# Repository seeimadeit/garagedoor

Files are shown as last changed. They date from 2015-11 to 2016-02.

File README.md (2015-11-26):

# Garage Door Opener

Project Status: Unstable - in development

 * circuit design - stable
* iphone software - unstable
* arduino software - unstable
* box housing - stable/regular changes

Project located @ 
[https://github.com/seeimadeit/garagedoor](https://github.com/seeimadeit/garagedoor "Github")
and [https://seeimadeit.wordpress.com/](https://seeimadeit.wordpress.com/ "Wordpress")

This hardware device is a simple Arduino based relay controller, it uses the Adafruit BLE nRF8001 [http://www.adafruit.com/products/1697](http://www.adafruit.com/products/1697 "Adafruit website").

Stuff I use to make it

* Hardware
	1. circuitboard Eagle CAD 7.4.0
	2. Housing Cubify Design 2014
* Software
	1. Apple XCode 7.1.x, Swift 2 - iPhone
	2. Arduino 1.6.5
	3. Libraries
		* MD5 - https://github.com/scottmac/arduino
		* BLE - https://github.com/sandeepmistry/arduino-BLEPeripheral

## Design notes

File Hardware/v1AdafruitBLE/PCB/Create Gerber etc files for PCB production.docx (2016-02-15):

Create Gerber etc files for PCB production

In eagle select the “Cam processor” from the File menu

After the cam processor has loaded from the File menu choose Open->Job

Load the garagedoor-gerb274x.cam file

The will be multiple tabs , each tab represents a section (or a file output).

It will look like this

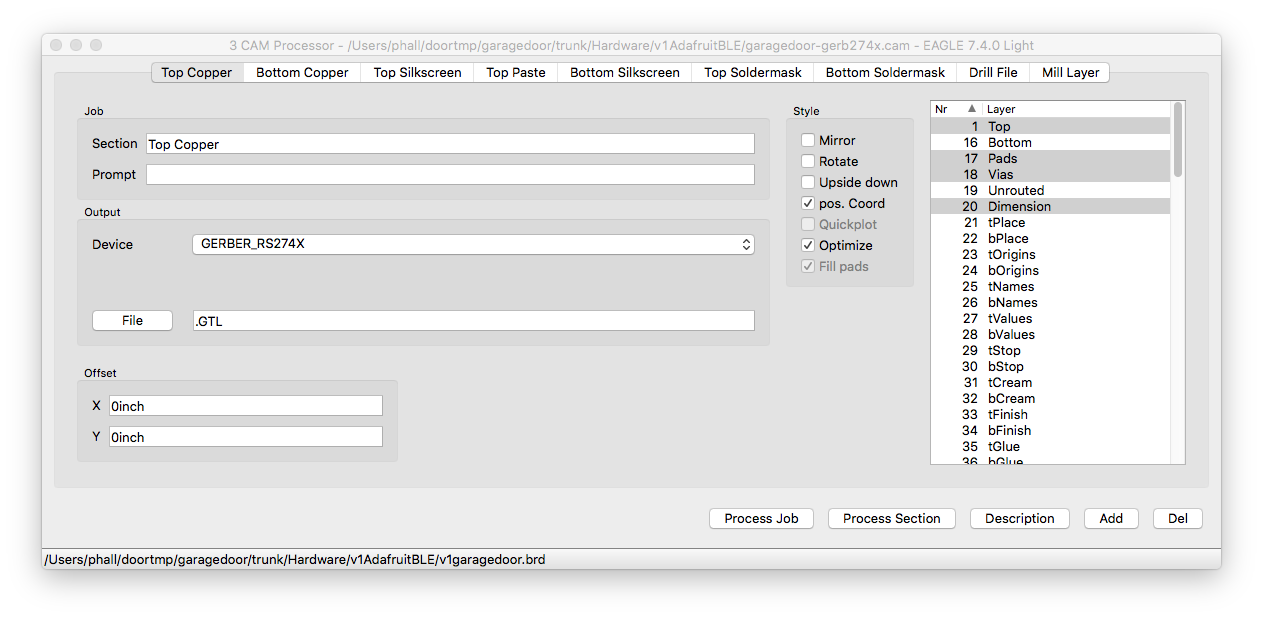
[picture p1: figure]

Click on each of the tab and review the settings to match the list below.

Click the ‘Process Job’ button to output the files.

Add the following files into a .ZIP file

V1garagedoor.dri

V1garagedoor.GBL

V1garagedoor.GBO

V1garagedoor.GBS

V1garagedoor.GML

V1garagedoor.GTL

V1garagedoor.GTO

V1garagedoor.GTP

V1garagedoor.GTS

V1garagedoor.TXT

Submitting to advanced circuits

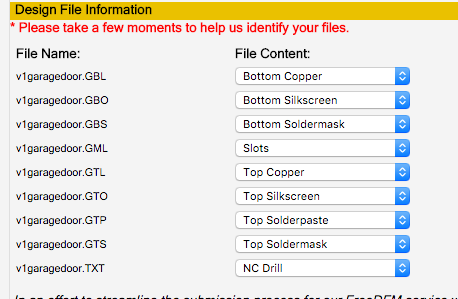
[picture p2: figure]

not sure

if the .GML file which is the milling – board cutout – is correctly set for slots.

If the .dri file is required so I’ve not included it here.

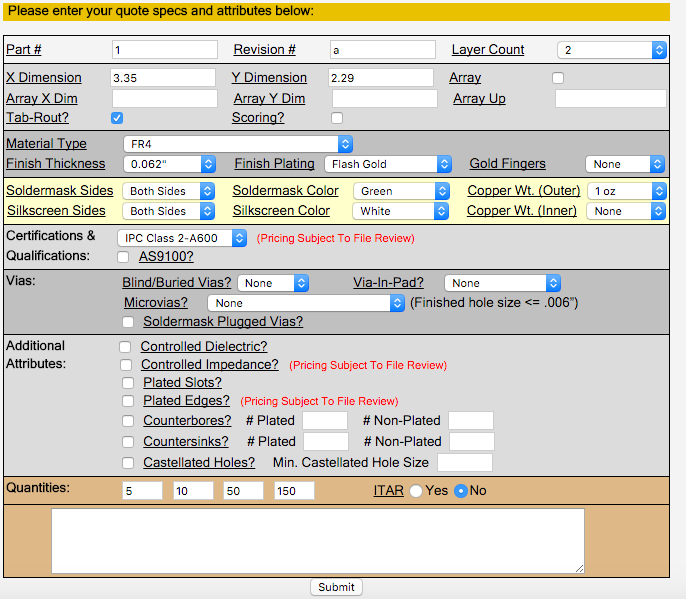
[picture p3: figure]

Top Copper

Job

Section: Top Copper

Output

Device: GERBER_RS274X

File : .GTL

Style

Pos.Coord, Optimize

Layers

1 Top, 17 Pads, 18 Vias, 20 Dimension

Bottom Copper

Job

Section : Bottom Copper

Output: GERBER_RS274X

File: .GBL

Style

Pos. Coord, Optimize

Layers

16 Bottom, 17 Pads, 18 Vias

Top Silkscreen

Job

Section: Top Silkscreen

Output

Device: GERBER_RS274X

File: .GTO

Style

Pos.Coord, Optimize

Layers

21 tPlace, 121 _tsilk

Top Paste (not included in the cam file because we do not need a solder stencil)

Job

Section: Top Paste

Output

Device: GERBER_RS274X

File: .GTP

Style

Pos. Coord, Optimize

Layers

31 tCream

Bottom Silkscreen

Job

Section: Bottom Silkscreen

Output

Device: GERBER_RS274X

File: .GBO

Style

Pos.Coord, Optimize

Layers

22 bPlace,122 _bsilk

Top Soldermask

Job

Section: Top Soldermask

Output

Device: GERBER_RS274X

File: .GTS

Style

Pos.Coord, Optimize

Layers

29 tStop

Bottom Soldermask

Job

Section: Bottom Soldermask

Output

Device: GERBER_RS274X

File: .GBS

Style

Pos.Coord, Optimize

Layers

30 bStop

Drill File

Job

Section: Drill File

Output

Device: EXCELLON

File: .TXT

Style

Pos. Coord,Optimize

Layers

44 Drills, 45 Holes

Mill Layer

Job

Section: Mill Layer

Output

Device: GERBER_RS274X

File: .GML

Style

Pos.Coord, Optimize

Layer

46 Milling

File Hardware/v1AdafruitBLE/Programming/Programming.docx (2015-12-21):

The microcontroller does not do anything without a program, in this document we show you how to program the device using a R3 Arduino.

We are going to use the ICSP or in circuit serial programing interface of the atmega328 controller.

The instructions and program for turning your Arduino into a ISP or in-system programmer are included in the Arduino IDE examples.

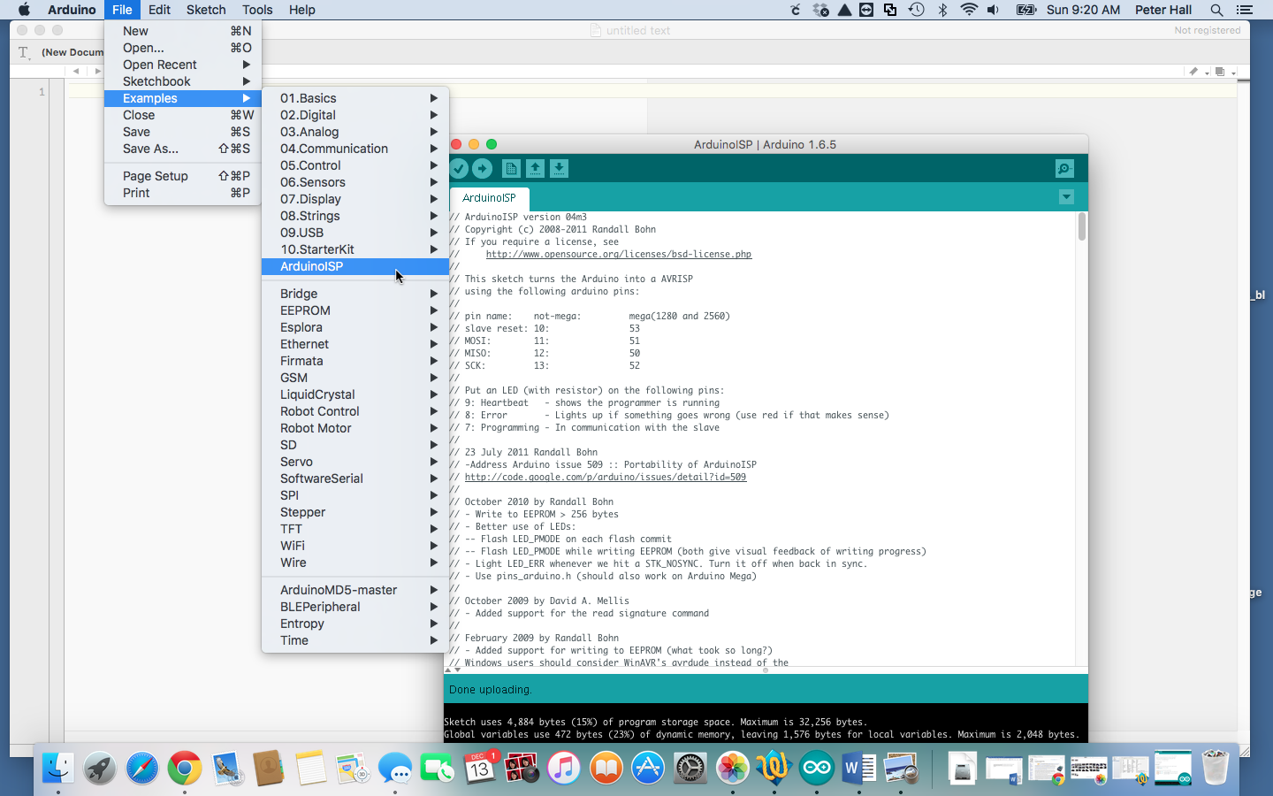
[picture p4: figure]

From the Menu choose File->Examples->ArduinoISP

You will need to make a minimum of 5 connections from the Arduino to the Garagedoor opener circuit.

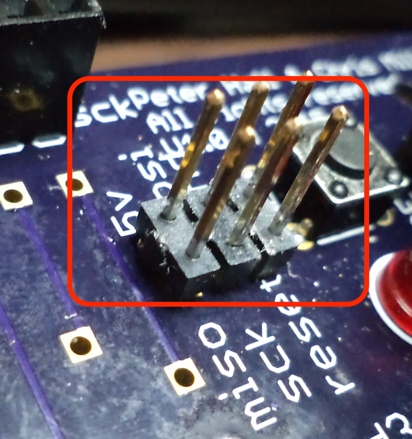
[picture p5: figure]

Connect the following using jumper leads.

Arduino pin | Garagedoor header
10 | Reset
11 | Mosi
12 | Miso
13 | Sck
GND | Gnd

After you have wired up the the connections. Consider making a permanent cable, it will make things more easy and you can reuse the cable for other projects. I glued the jumper cables with super glue, added some labels so I know how to plug it in and then to make it look good I added heat shrink tubing.

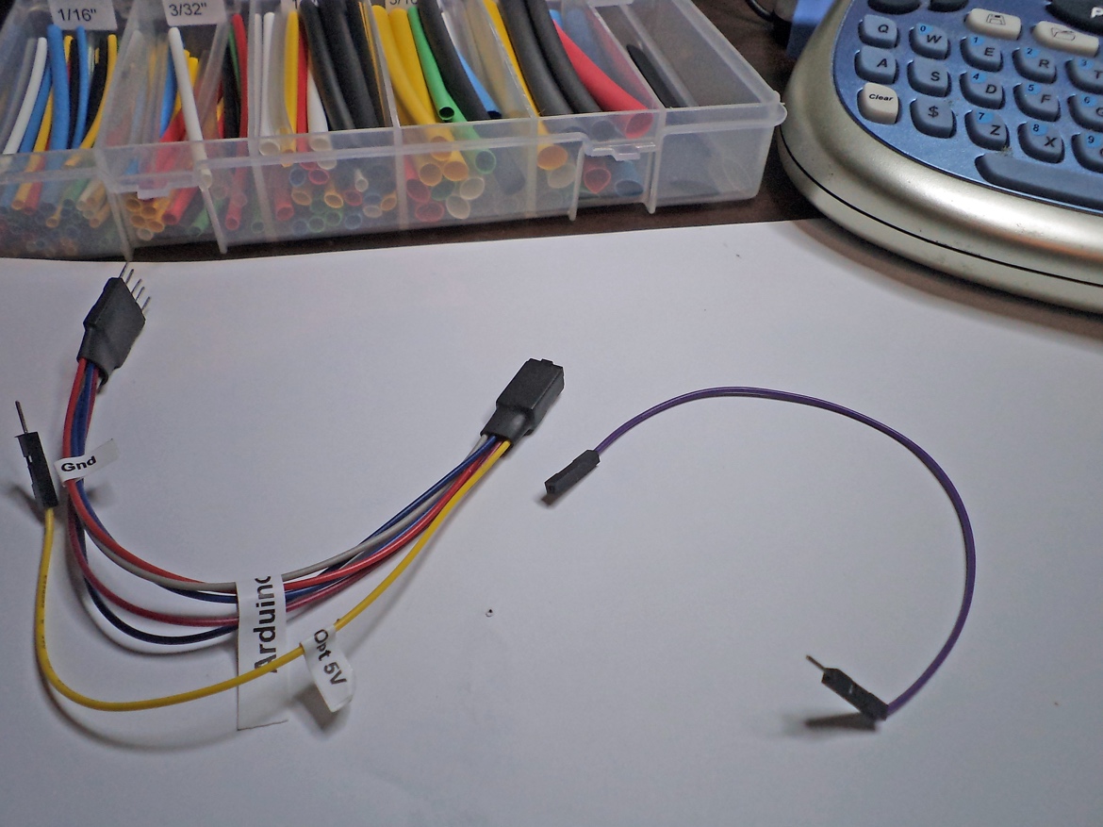
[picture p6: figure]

I added an extra 5V optional cable so I ca use it for another project. You don’t need the 5V cable for this project as the board must be powered by an external power supply.

Be very careful with the superglue, or you might stick the cable to the header.

When it’s plugged in it should look something like this

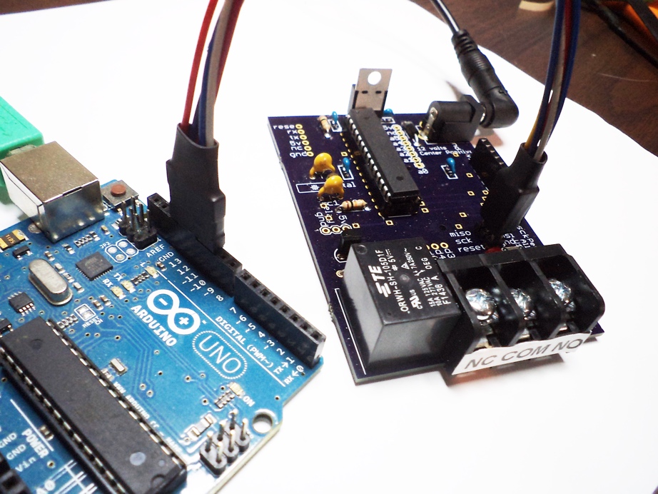
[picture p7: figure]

First we need to program the Arduino as an ISP.

Make sure your Arduino is plugged into the USB and your computer. You have already configured your Arduino software (If not consult the Arduino website if you need help)

In the window with ArduinoISP click on the arrow as in the image. You will notice when you mouse over the arrow the text Upload appears to the right.

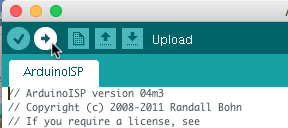
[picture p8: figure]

After the upload has completed it will say ‘Done’.

To program the garagedoor opener we need to change the software to use the Arduino as the programmer.

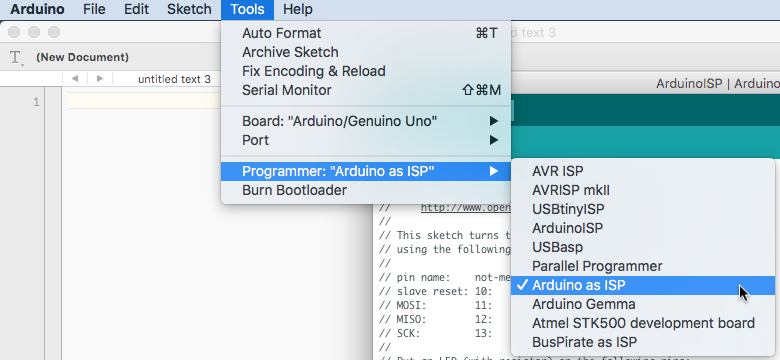
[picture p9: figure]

From the menu choose Tool->Programmer:->Arduino as ISP

The Arduino needs to be configured with some hardware fuses. We can’t do that directly with the Arduino software but we can program the garage door opener with the Arduino bootloader which will set the hardware fuses for us. This only needs to happen one time. If you bought your atmega328 chip directly it will not contain the settings. However if you got your chip with a kit it will already contain the settings so you won’t need to do this step.

To install the bootloader , first make sure the Arduino is plugged in to the USB, then make sure the Garagedoor opener is plugged into the Arduino.

From the tools Menu choose ‘Burn Boatloader’. When the boatloader has been written to the chip it will say its’ ‘Done’.

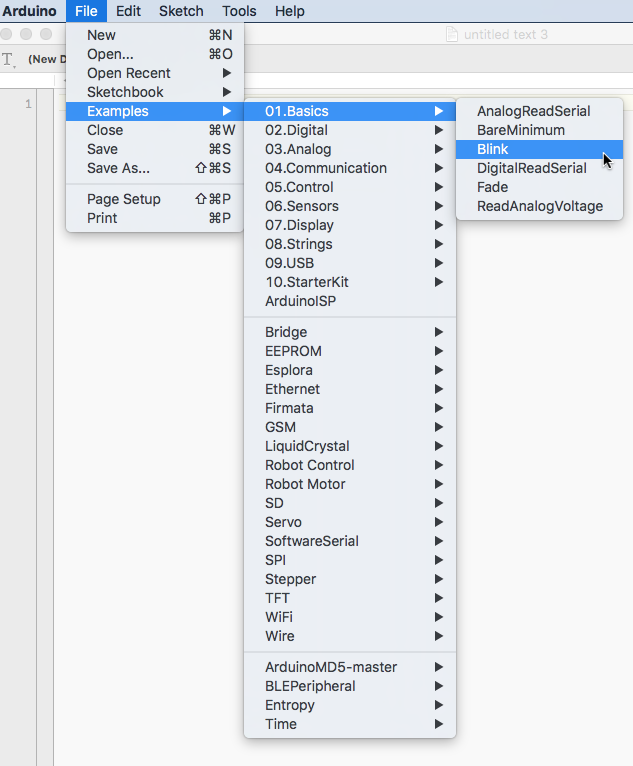
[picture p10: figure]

Now we have an Arduino ready to install the Garage door opener software. But before we do that, lets run a simple test so see if the chip is working.

From the menus choose File->Examples->01.Basics->Blink

Change the program so it looks like this:

/*

Blink

Turns on an LED on for one second, then off for one second, repeatedly.

Most Arduinos have an on-board LED you can control. On the Uno and

Leonardo, it is attached to digital pin 13. If you're unsure what

pin the on-board LED is connected to on your Arduino model, check

the documentation at http://www.arduino.cc

This example code is in the public domain.

modified 8 May 2014

by Scott Fitzgerald

*/

#define PIN 6

// the setup function runs once when you press reset or power the board

void setup() {

// initialize digital pin as an output.

pinMode(PIN, OUTPUT);

}

// the loop function runs over and over again forever

void loop() {

digitalWrite(PIN, HIGH); // turn the LED on (HIGH is the voltage level)

delay(1000); // wait for a second

digitalWrite(PIN, LOW); // turn the LED off by making the voltage LOW

delay(1000); // wait for a second

}

The garage door opener has an LED on digital pin 6 not pin 13. Now we are ready to upload this to the garage door opener.

This time we will use the Arduino to program the garage door opener.

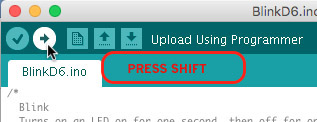
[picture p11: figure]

Press and hold down the shift key, then click on the arrow, make sure it says ‘Upload Using Programmer’ before you click or you will rewrite the Arduino with the blinking LED program.

If all goes well, the LED on the garage door opener will start to blink.

That’s all there is to it to program the device. Now let look at what you need to build the garage door opener.

Garage door opener firmware.

The garage door opener firmware relies of the work of others. In the case of the Arduino we need to install the libraries into the Arduino Libraries folder.

We need 2 libraries

1) BLEPeripheral v0.1.5
2) ArduinoMD5

The libraries need to be installed into the Libraries folder for you Arduino Sketchbook location. (see below for more information)

### Download Library

#### Arduino

#### Using the Arduino IDE Library Manager

1. Choose Sketch -> Include Library -> Manage Libraries...
2. Type BLEPeripheral into the search box.
3. Click the row to select the library.
4. Click the Install button to install the library.

#### Using Git

cd ~/Documents/Arduino/libraries/

git clone https://github.com/sandeepmistry/arduino-BLEPeripheral BLEPeripheral

source code is available from here

https://github.com/sandeepmistry/arduino-BLEPeripheral

ArduinoMD5

https://github.com/tzikis/ArduinoMD5

Download a ZIP file from the above address.

Unzip the file and move into your Arduino sketchbook location.

Look for the “Sketchbook location” field in the Preferences dialog.

If you have not changed the default it will be in your Documents/Arduino folder.

To find your Sketchbook location for a mac.

Click on the Arduino application menu and choose Preferences.

To find your Sketchbook location for windows

Click on the File menu and choose Preferences.

Make sure you close the Arduino software and reload for the libraries to become available.

You will now be able to compile and install the Garage Door Opener firmware.

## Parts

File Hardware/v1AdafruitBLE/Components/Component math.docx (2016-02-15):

Component maths

R4 – current limiting base transistor

2K4 Ω

The relay has a coil resistance of 70Ω. So the current draw will be

I = V ÷ R

0.07A = 5v ÷ 70Ω

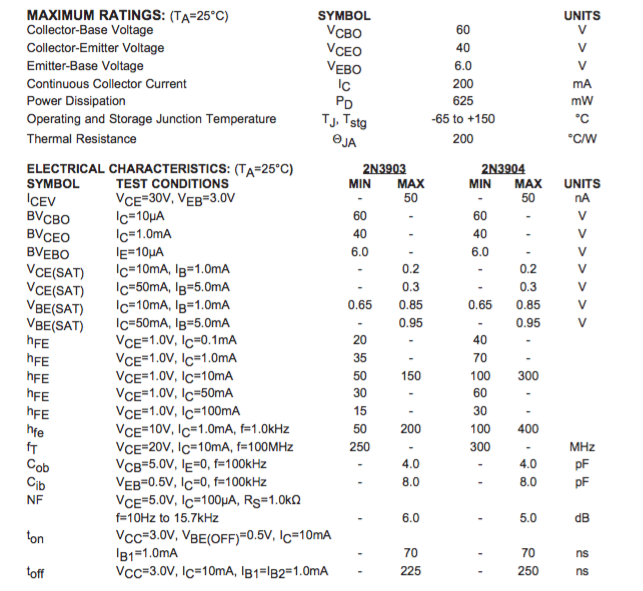
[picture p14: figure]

2N3904 datasheet

Calculate the base resistor

Supply HFE,VIN,VBE from the datasheet and your IC from your circuit
| A | mA | uA
IC | 0.07 | 70 | 70000
HFE | 45
IB | 0.001555556 | 1.555555556 | 1555.555556
VIN | 5
VBE | 0.95
RB | 2603.571429

Transistor base current

IB = (Ic)/(hfe) = (7mA)/45 = 1.5mA

Transistor Base resistance

RB = (Vin-VBE)/(IB) = (5v-0.95v)/0.0015 = 2603Ω

Closest standard value resistor 2K4Ω

Reference:

http://www.electronics-tutorials.ws/transistor/tran_4.html

R3 – current limiting led

I didn’t base these values from a datasheet. I used common values.

Calculate series resistor

Supply VF,IF from the led datasheet and VS for your circuit
| | mA
VS | 5
VF | 1.8
IF | 0.014 | 14
RS | 228.5714286

Reference:

http://www.electronics-tutorials.ws/diode/diode_8.html

R1 – pull up reset button

In the atmega328 datasheet it says

24.3 Physical Interface

Pull-up resistors on the dW/(RESET) line must not be smaller than 10kΩ.

R2 – pull up prog button

Copied from R1, if it works for the reset it will work for any other button.

C4/C5 power regulator caps

0.33uF – taken from the example in the datasheet. Note the datasheet recommends

A 0.33 mF or larger tantalum, mylar, or other capacitor having low internal impedance at high frequencies should be chosen.

I ignored that advise and used the multilayer ceramic caps. I did that because the regulator datasheet says they are optional; so adding them in is probably better than not having them.

But tantulum are crazy expensive

C7/C6 decoupling caps

A normal decouping cap is 0.1uF or 0.01uF, I have used 0.1uF.

Sparkfun have a good description of decoupling caps here: https://learn.sparkfun.com/tutorials/capacitors/application-examples

C2/C1 crystal

I choose 20pF using a Cstray value of 10pF because I don’t have a clue and the crystal is a little distance from the uC.

Reference: https://blog.adafruit.com/2012/01/24/choosing-the-right-crystal-and-caps-for-your-design/

D1 – diode reverse power protection

1N4004

could have used 1N4001 and it would work just the same. But I choose a 400V protection because I need a coil flyback diode. So I reused the same diode here.

D2 – diode flyback relay

Provided 400V reverse DC blocking voltage. Because the relay is a coil I wanted to be extra sure. I think a 1N4001 would also work just as well.

RELAY – the relay

Chosen because I wanted a small size relay. It provided 10A rating which is plenty good enough for a garage door opener. It works on upto VAC 227, and upto 28VDC. So it has a good overall usage,

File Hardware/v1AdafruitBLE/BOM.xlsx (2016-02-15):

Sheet: Parts
Part | Value | Device | Package | Description | MANF | MOUSER | Required | Optional | unit cost | product cost | DIGIKEY | Unit Cost | product cost
C1/C2 | 33pF | CAPPTH1 | CAP-PTH-5MM | 33pF Capacitor | 1C10C0G330J050B | 75-1C10C0G330J050B | 2 |  | 0.15 | 0.30 | 1265PH-ND | 0.31 | 0.62
C6/C7 | 0.1uF |  |  | 0.1uF Capacitor decoupling | 21RZ310-RC | 21RZ310-RC | 2 |  | 0.08 | 0.16 | 478-5741-ND | 0.24 | 0.48
C3/C4 | .33uF | CAPKIT | CAP-PTH-SMALL-KIT | 0.33uF Capacitor | FK18X7R1E334K | 810-FK18X7R1E334K | 2 |  | 0.31 | 0.62 | 445-5306-ND | 0.32 | 0.64
D1/D2 | 1N4004 | 1N4004 | DO41-10 | DIODE | 1N4004-T | 621-1N4004 | 2 |  | 0.13 | 0.26 | 1N4004DICT-ND | 0.13 | 0.26
IC1 | 7805 | 78V | TO220V | Positive VOLTAGE REGULATOR 5v | NCP7805TG | 863-NCP7805TG | 1 |  | 0.47 | 0.47 | MC7805CTGOS-ND | 0.45 | 0.45
JP1 | ISP | M03X2NO_SILK | 2X3-NS | 2x3 .1 header." | 5-146252-3 | 571-5-146252-3 | 1 |  | 0.42 | 0.42 | 5-146252-3-ND | 0.42 | 0.42
JP2 | adafruit nrf8001 | M10SILK_FEMALE_PTH | 1X10 | Header 10, .1 female | 10Fx1-254mm | 992-10FX1-254MM | 1 |  | 0.70 | 0.70 | SAM1119-10-ND | 1.06 | 1.06
JP3 | programmer | M06NO_SILK_FEMALE_PTH | 1X06_NO_SILK | Header 6 |  |  | 0 | 1 |  | 0.00 |  |  | 0.00
JP4 | test point relay | M03LOCK | 1X03_LOCK | Header 3 |  |  | 0 | 1 |  | 0.00 |  |  | 0.00
JP5 | analog pins | M08SILK_FEMALE_PTH | 1X08 | Header 8 |  |  | 0 | 1 |  | 0.00 |  |  | 0.00
JP7 | digital pins | M06NO_SILK_FEMALE_PTH | 1X06_NO_SILK | Header 6 |  |  | 0 | 1 |  | 0.00 |  |  | 0.00
JP8 | screw terminal | M03SCREW | SCREWTERMINAL-3.5MM-3 | Header 3 |  |  | 0 | 1 |  | 0.00 |  |  | 0.00
LED | 5mm | LED5MM | LED5MM | LED green 1.8Fv 5mm round bulb | LTL2R3KGD-EM | 859-LTL2R3KGD-EM | 1 |  | 0.08 | 0.08 | 160-1852-ND | 0.30 | 0.30
Q1 | 2N3904 | TRANSISTOR_NPN2N3904 | TO-92 | Generic NPN BJT | 2N3904BU | 512-2N3904BU | 1 |  | 0.19 | 0.19 | 2N3904FS-ND | 0.18 | 0.18
R1/R2 | 10K | RESISTORAXIAL-0.3 | AXIAL-0.3 | 10K Resistor | CFR-25JR-52-10K | 603-CFR-25JR-5210K | 2 |  | 0.10 | 0.20 | 10KQBK-ND | 0.10 | 0.20
R4 | 2.4K | RESISTORAXIAL-0.3 | AXIAL-0.3 | 2K4 Resistor | 291-2.4K-RC | 291-2.4K-RC | 1 |  | 0.10 | 0.10 | CF14JT2K40CT-ND | 0.10 | 0.10
R3 | 220 | RESISTORAXIAL-0.3 | AXIAL-0.3 | 220 Resistor | CFR-25JR-52-220R | 603-CFR-25JR-52220R | 1 |  | 0.10 | 0.10 | CF14JT220RCT-ND | 0.10 | 0.10
RELAY | relay | ZF112 | ZF112 | RELAY | ORWH-SH-105D1F,000 | 655-ORWH-SH105D1F000 | 1 |  | 1.22 | 1.22 | PB2032-ND | 1.46 | 1.46
S3 | SWITCH-MOMENTARY-2PTH | SWITCH-MOMENTARY-2PTH | TACTILE-PTH | Various NO switches- pushbuttons, reed, etc | 1301.9301 | 693-1301.9301 | 2 | 0 | 0.28 | 0.56 | 1301.9301-ND,486-1943-ND | 0.36 | 0.72
U$1 | 2.1MMJACKTHM | 2.1MMJACKTHM | PJ-102A | 2.1mm x 5.5mm THM DC jack with internal switch. Digikey part #PJ-102A, 4UCON part #05537 | CON-SOCJ-2155 | 992-CON-SOCJ-2155 | 1 |  | 1.00 | 1.00 | CP-102A-ND | 1.00 | 1.00
U1 | ATMEGA328P_PDIP | ATMEGA328P_PDIP | DIL28-3 | uC used in the Arduino | ATMEGA328P-PU | 556-ATMEGA328P-PU | 1 |  | 3.70 | 3.70 | ATMEGA328P-PU-ND | 3.70 | 3.70
X1 | 16mhz | CRYSTALTC38H | TC38H | 16 MHz ECS Crystal 20pF | ECS-160-20-46X | 520-160-20-46X | 1 |  | 0.46 | 0.46 | XC1759-ND | 0.46 | 0.46
 |  |  |  | Bluetooth / 802.15.1 Development Tools Bluetooth Low Energy nRF8001 breakout | 1697 | 485-1697 | 1 |  | 19.95 | 19.95 | 1528-1199-ND | 19.95 | 19.95
 |  |  |  | Barrier Terminal Blocks 3P TRI-BARRIER .375" | 6PCV-03-006 | 571-514376524 | 1 |  | 1.42 | 1.42 | A98482-ND | 1.42 | 1.42
 |  |  |  | IC & Component Sockets SOCKET 28POS .3" IC OPEN FRAME | 4828-3004-CP | 517-4828-3004-CP | 1 |  | 0.77 | 0.77 | 3M5480-ND | 0.77 | 0.77
 |  |  |  | Circuit Board |  | v1garagedoor.brd | 1 |  | 13.22 | 13.22 |  |  | 13.22
 |  |  |  |  |  |  |  |  |  | 45.90 |  |  | 47.51
 |  |  |  | OSH Park |  |  |  |  | 39.66

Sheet: actual costs
percent profit |  | cost per unit |  | sale price | substitute part | part | units | unit cost (100 min) | total | single unit cost | cost saving
13.82 |  | 30.72 |  | 45.00 |  | Circuit boards | 100 | 4.1257 | 412.57 | 13.3559 | 9.2302
 | 100 units cost price | 3071.57 | 100 units sale price | 4500.00 |  | 75-1C10C0G330J050B | 100 | 0.1170 | 11.70 | 0.1500 | 0.0330
 |  |  |  |  |  | 21RZ310-RC | 100 | 0.0690 | 6.90 | 0.0800 | 0.0110
 | 100 units profit | 1428.43 |  |  |  | 810-FK18X7R1E334K | 100 | 0.1000 | 10.00 | 0.3100 | 0.2100
 | profit / unit cost | 46.50488187 |  |  |  | 621-1N4004 | 100 | 0.0380 | 3.80 | 0.1300 | 0.0920
 |  |  |  |  |  | 863-NCP7805TG | 100 | 0.2220 | 22.20 | 0.4700 | 0.2480
 |  |  |  |  |  | 571-5-146252-3 | 100 | 0.4140 | 41.40 | 0.4200 | 0.0060
 |  |  |  |  |  | 992-10FX1-254MM | 100 | 0.6830 | 68.30 | 0.7000 | 0.0170
 |  |  |  |  |  | 859-LTL2R3KGD-EM | 100 | 0.0600 | 6.00 | 0.0800 | 0.0200
 |  |  |  |  |  | 512-2N3904BU | 100 | 0.0570 | 5.70 | 0.1900 | 0.1330
 |  |  |  |  |  | 603-CFR-25JR-5210K | 100 | 0.0130 | 1.30 | 0.1000 | 0.0870
 |  |  |  |  |  | 291-2.4K-RC | 200 | 0.0190 | 3.80 | 0.1000 | 0.0810
 |  |  |  |  | 588-ON2215E-R58 | 603-CFR-25JR-52220R | 100 | 0.0620 | 6.20 | 0.1000 | 0.0380
 |  |  |  |  |  | 655-ORWH-SH105D1F000 | 100 | 1.1000 | 110.00 | 1.2200 | 0.1200
 |  |  |  |  | 693-1301.9303 | 693-1301.9301 | 100 | 0.1740 | 17.40 | 0.2100 | 0.0360
 |  |  |  |  | 502-RAPC722X | 992-CON-SOCJ-2155 | 100 | 0.8200 | 82.00 | 1.0000 | 0.1800
 |  |  |  |  |  | 556-ATMEGA328P-PU | 100 | 2.7100 | 271.00 | 3.7000 | 0.9900
 |  |  |  |  |  | 520-160-20-46X | 100 | 0.2600 | 26.00 | 0.4600 | 0.2000
 |  |  |  |  |  | 485-1697 | 10 | 17.9600 | 179.60 | 19.9500 | 1.9900
 |  |  |  |  |  | 571-514376524 | 100 | 1.1600 | 116.00 | 1.4200 | 0.2600
 |  |  |  |  |  | 517-4828-3004-CP | 100 | 0.5520 | 55.20 | 0.7700 | 0.2180
 |  |  |  |  |  |  |  | 30.7157 | 1457.07 | 44.9159 | 14.2002
 |  |  |  |  | miscellaneous items
 |  |  |  |  | anti-static sponge | 809-37705 | 1 | 67.5400 | 67.54
 |  |  |  |  | anti-static bag | 517-10046 | 1 | 6.06 | 6.06

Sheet: crystal caps
Reference: | https://blog.adafruit.com/2012/01/24/choosing-the-right-crystal-and-caps-for-your-design/
choosing the right caps, supply the stray capacitance, then the C1 and C2 capacitance, CL will be the datasheet Load Capacitance
 | pF
Cstray | 4
C1 | 34
C2 | 34
CL | 21 |  | try to get this value as close to the datasheet CL value
Use this to get you started, enter the Cstray and the datasheet CL value
Rule of thumb estimate
Cstray | 4
CL | 20
 | 32
 |  | Cstray should be somewhere around 2pF to 5pF

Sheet: led series resistor
Reference: | http://www.electronics-tutorials.ws/diode/diode_8.html
Calculate series resistor
Supply VF,IF from the led datasheet and VS for your circuit
 |  | mA
VS | 5
VF | 1.8
IF | 0.014 | 14
RS | 228.5714286
Calculate forward Current
 |  | mA | uA
VS | 5
VF | 1.8
RS | 220
IF | 0.01454545455 | 14.54545455 | 14545.45455

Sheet: base resistor calc
Transistor as a Switch
Reference : | http://www.electronics-tutorials.ws/transistor/tran_4.html
Calculate the base resistor
Supply HFE,VIN,VBE from the datasheet and your Ic from your circuit
 | A | mA | uA
IC | 0.07 | 70 | 70000
HFE | 45
IB | 0.001555555556 | 1.555555556 | 1555.555556
VIN | 5
VBE | 0.95
RB | 2603.571429
watts | 0.007777777778

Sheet: convert amps
Amps | mA | uA
1 | 1000 | 1000000
0.7 | 700 | 700000
0.07 | 70 | 70000
0.007 | 7 | 7000
0.0007 | 0.7 | 700
7e-05 | 0.07 | 70
7e-06 | 0.007 | 7
0.03333 | 33.33 | 33330

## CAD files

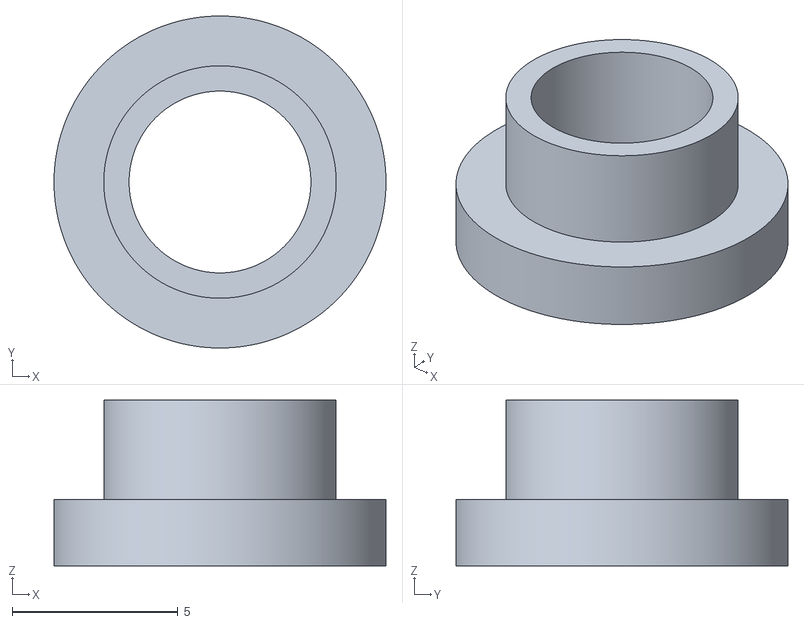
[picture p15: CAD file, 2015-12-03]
Hardware/v1Housing/pushbutton_limiter.stl
10.0 x 10.0 x 5.00

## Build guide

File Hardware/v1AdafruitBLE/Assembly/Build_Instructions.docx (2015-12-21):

Beginner soldering level

The document describes in easy to read format, steps to correctly solder the garagedoor circuit. See http://seeimadeit.wordpress.com

# About the board

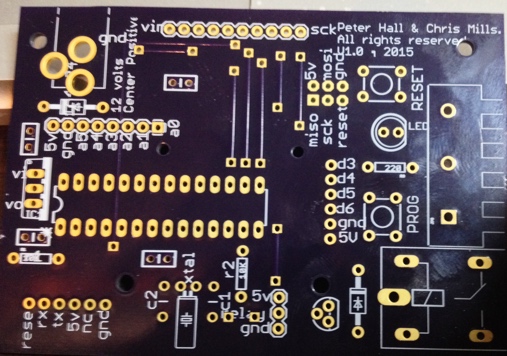
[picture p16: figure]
Components are placed on this side of the board.

This is the side to place the components.

Figure 1 Component Side

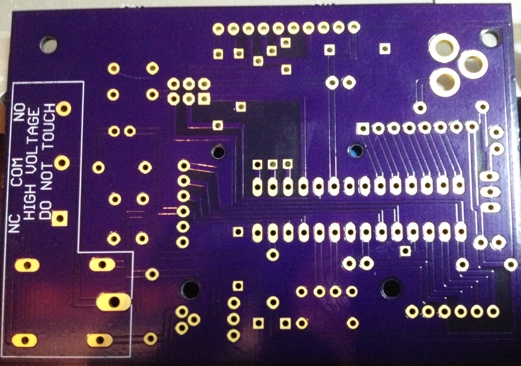
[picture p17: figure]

This is where we will solder the components to the board

Figure 2 Solder Side

1. Crystal (1)

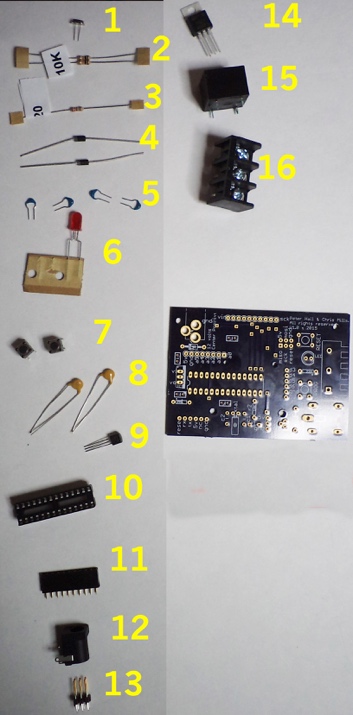
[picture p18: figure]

2. 10K resistor (2)
3. 220 resistor (1)
4. 1n4004 diode (2)
5. 0.33uF Cap (4)
6. 5mm LED (1)
7. micro switch (2)
8. 20pF Cap (2)
9. NPN BJT (1)
10. IC Socket (1)
11. 10 pin header (1)
12. Power Jack (1)
13. 6 pin header (1)
14. 5V regulator (1)
15. relay (1)
16. terminal block (1)

Figure 3 Solder component sequence

# Tools required

Soldering iron with a reasonable size chisel type tip, recommended 2mm to 3mm wide, a conical type tip will not work well.

Solder – 0.5mm or less diameter, rosin core solder

Side cutters

## Optionally

solder wick (to clean up your mess)

rosin flux – if you find the solder doesn’t want to flow easy

sticky tape – to hold components in place

third hand device – to hold the circuit board while you solder

Headband magnifier – if your eyes aren’t the best

Rubbing alcohol & tooth brush – to clean off rosin

Pliers – to bend component legs

# The Build

## Crystal

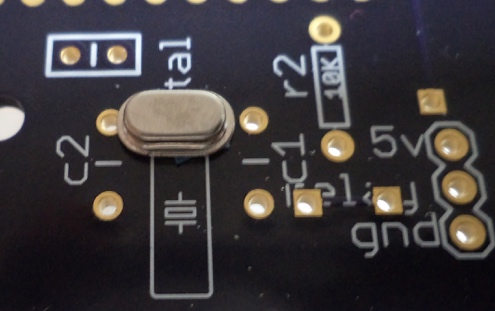
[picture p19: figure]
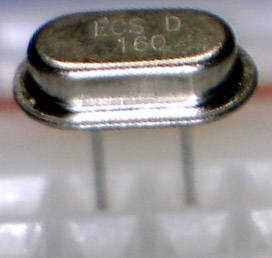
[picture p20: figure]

Start by inserting the crystal, it’s the smallest part of the circuit. Its best to work from smallest component to largest component, because larger components can get in the way. This crystal is very small and the pins are easy to break off. The circuit legend is actually showing a watch style crystal. It also has the word “xtal”.

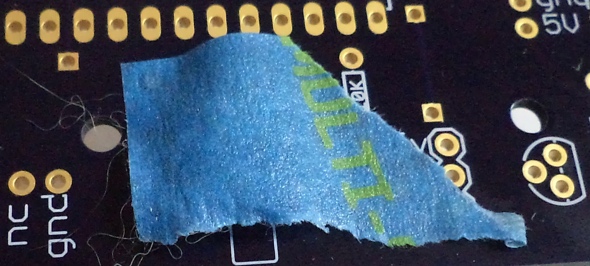
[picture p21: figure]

To hold the component in place I used tape to hold it whilst I flipped it over to solder. I also find chewing gum works in some cases.

## Resistors

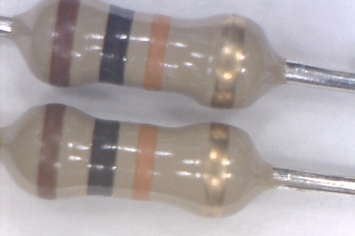
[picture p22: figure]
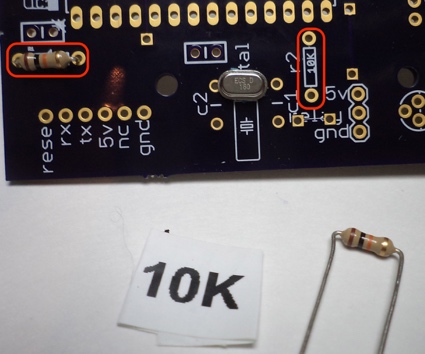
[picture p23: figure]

Insert the 2 10K resistors. Bend the pins over to fit the holes. The image shows the 2 locations in red.

Note the color of the resistors (google a resistor color code to understand the colors).

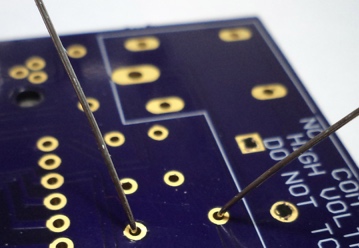
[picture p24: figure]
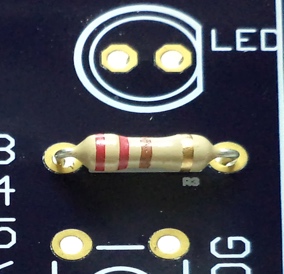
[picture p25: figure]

Insert the single 220 resistor, again bend the pins over to fit the holes.

You can also bend the pins on the solder side to hold the component in place.

## Diodes

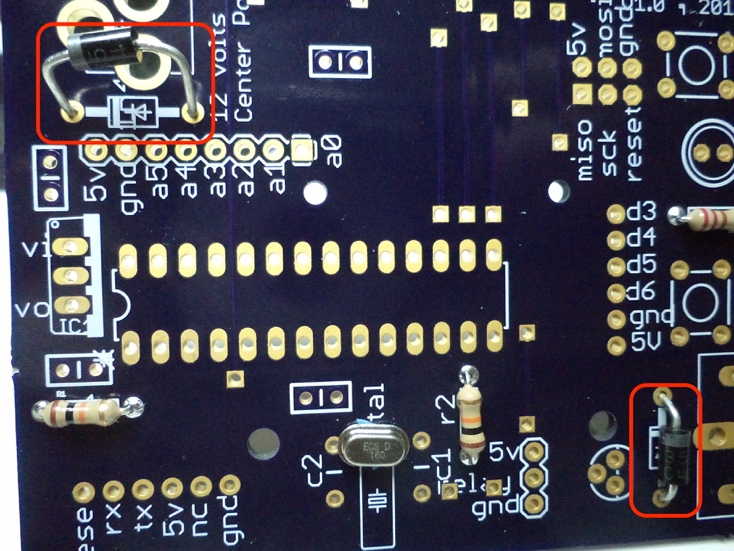
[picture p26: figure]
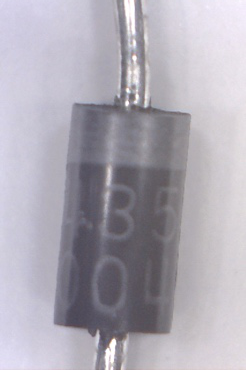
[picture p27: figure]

There are 2 diodes in the circuit. They are outlined in red. Note this component needs to be oriented correctly to work. Look at the circuit symbol there is a white bar highlighted in red. This represents the same on the component.

## Cleanup – time for a break

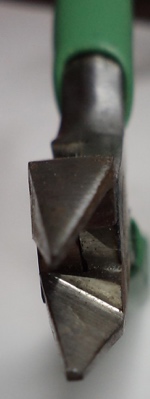
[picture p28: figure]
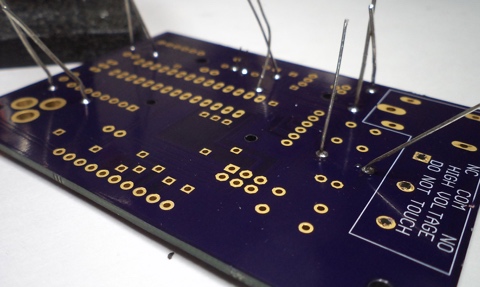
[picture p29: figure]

Time for cleanup, the solder side is requiring a trim. You want to remove the legs nice and tight against the board. Ideally you want to cut the legs just above the solder.

Use some sharp side cutters. The cutters will allow you to get close to the board. Notice the cutters are almost flat on one side.

## Capacitors

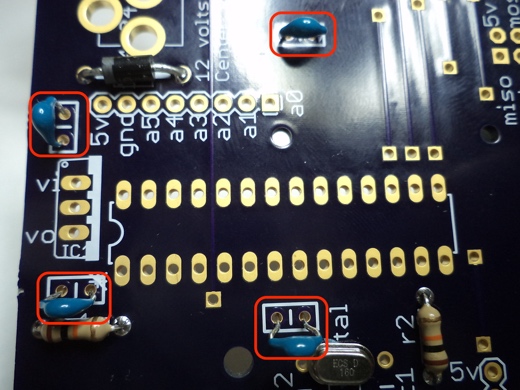
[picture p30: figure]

These small capacitors are 0.33uF (micro Farad), they are so small I can’t read the label on them.

There are 4 on the circuit, the 2 on the left of the picture are used to stabilize the linear regulator. The other 2 are used to decouple the micro controller. These capacitors are not the the ideal type to use for the regulator, but it was a choice to reuse components that are already used for the circuit, therefore saving a small amount of money. Making decisions like that can help keep the costs down on a product.

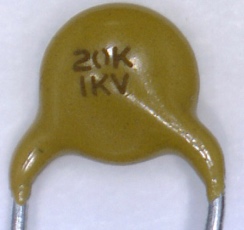
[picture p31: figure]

2 capacitors are used to ‘load’ the crystal, without them the crystal will not work. These capacitors are 20pF (pico Farad).

## Transistor

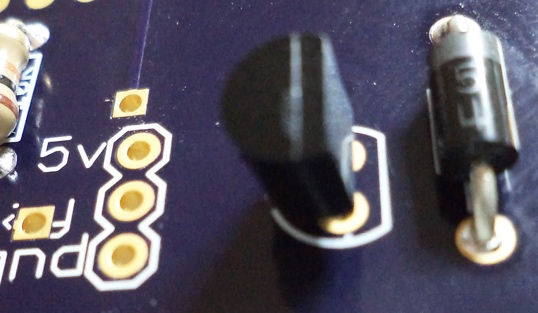
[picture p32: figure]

A single transistor is used on this circuit as a switch, the microcontroller will toggle the transistor on and off. We do this to protect the microcontroller from excessive current draw, which would damage the microcontroller.

Notice the shape of the transistor and the symbol on the circuit board. The component has 3 pins called E (emitter), B (base) and C (collector). It’s important the pins are correctly positioned on the circuit board for it to work.

## LED – turn on the lights

This LED is used to give some visual feedback, in this device its used by the developer to indicate something in the firmware. When designing it’s important that you think about how it’s going to be tested.

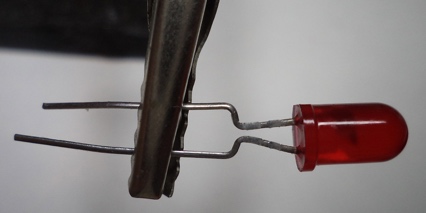
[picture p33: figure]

The LED needs to be orientated correctly to work. There are 2 ways to identify the anode (+) and cathode (-), If your LED still has it legs intact the long leg is the anode, also the LED has a flat on the bottom of the bulb. See in the image only one side appears to have a ledge. Look at the circuit board and match the flat side of the LED to the symbol.

Notice on the circuit board, there is a resistor connected to the LED, this is called a current limiting resistor, its there to stop the LED drawing to much current from the micro controller.

## Buttons – human interface

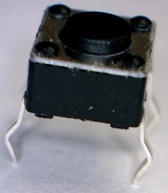
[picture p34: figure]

The push button pins are bent to form a rectangle; this is because the buttons need to be installed in the correct orientation. Insert them and solder in place. There are 2 as shown in the red outline.

## Chip and sockets

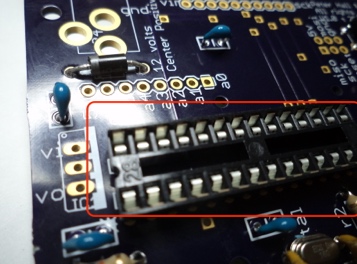
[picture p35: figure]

Moving to the larger components, the 28 pin IC socket, which is optional allows you to change out the chip, it’s a convenience feature I like to use for general purpose chips (if possible) because it allows me to reuse the chip for another project. If you choose not to install the socket you will need to solder the atmega328 ic. Notice the socket has a notch to indicate the first pin. The legend also has the same notch. Match the notches when you insert the component. The ic also has the notch and pin 1 is indicated with a dot above the pin. If you solder the ic directly make sure the notch matches the legend.

## Headers

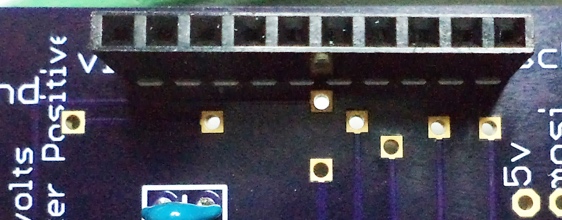
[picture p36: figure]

Nearly there, the 10 pin female header is used to connect the bluetooth module. I found holding this component with tape helped with the soldering.

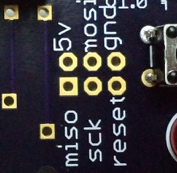
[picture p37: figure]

Add the last header, this is a 6 pin male header, we will need this to reprogram the microcontroller. It’s called an ICSP header.

## Power Jack

To finish up the soldering add the remaining components:

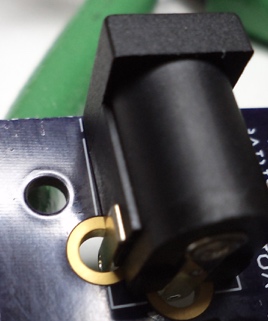
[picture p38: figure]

Power Jack, note this requires a 9v-12v 2.1mm power supply with a center positive jack. Most 6v supplies will also work if it’s not a regulated supply. Note the circuitboard holes are large for the component legs, you want to try and fill the holes, but be careful not to burn the plastic. So don’t leave the iron on the board for too long.

## Relay

The relay is used to connect and disconnect the power to the externally connected device, for example a lamp or a garage door opener. Rated for 10A for 227vac or 15A or 125vac. There’s plenty of other things you can control.

## Terminal block – interface to the external world

The terminal block is used to connect the external device you want to control.

It has 3 terminals

1) Normally open
2) Common
3) Normally closed

These states refer to the circuit, ie. Open circuit or closed circuit. In English if the state is normally open , it means the circuit is not complete so electricity will not flow. The word ‘normally’ means the state the device is in when no power to supplied to the actuator pin.

## Finished - What it should look like

Thats the soldering completed, plug in the bluetooth module and the microcontroller.

It should look like this.

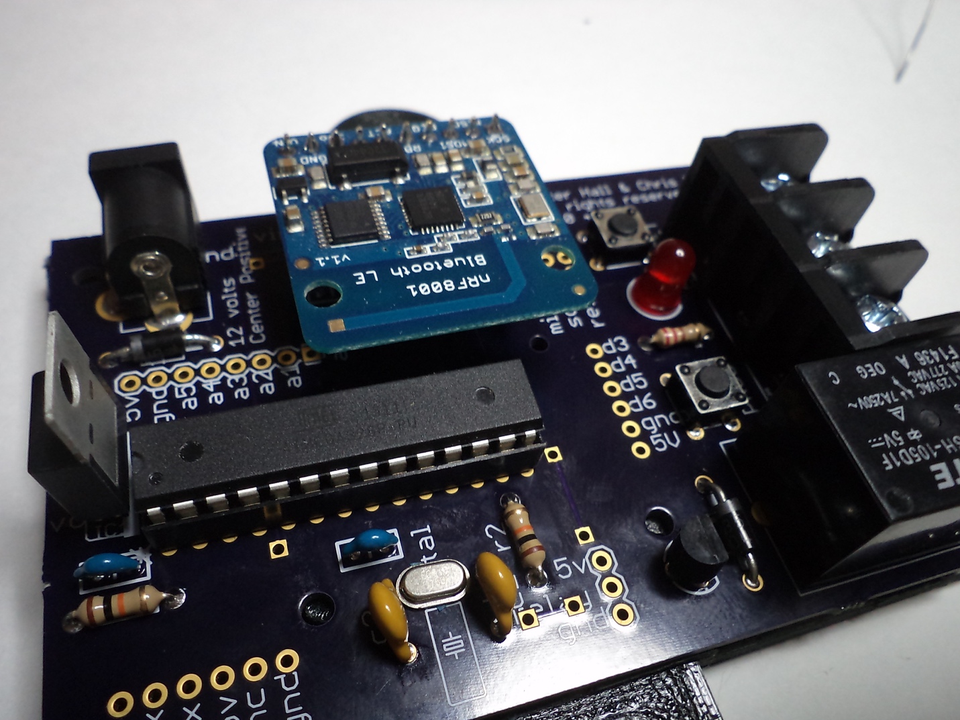
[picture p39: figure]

There are extra holes for headers, these holes can be used for experimenting. The legend references the pins as used by an Arduino.

Programming the device is covered in another article.

Your atmega328 microcontroller should already be programmed with the firmware, if you supply power to the unit you should see the LED glow momentarily, it will indicate its working.

Congratulations, you have made your device.

Garage door opener build instructions

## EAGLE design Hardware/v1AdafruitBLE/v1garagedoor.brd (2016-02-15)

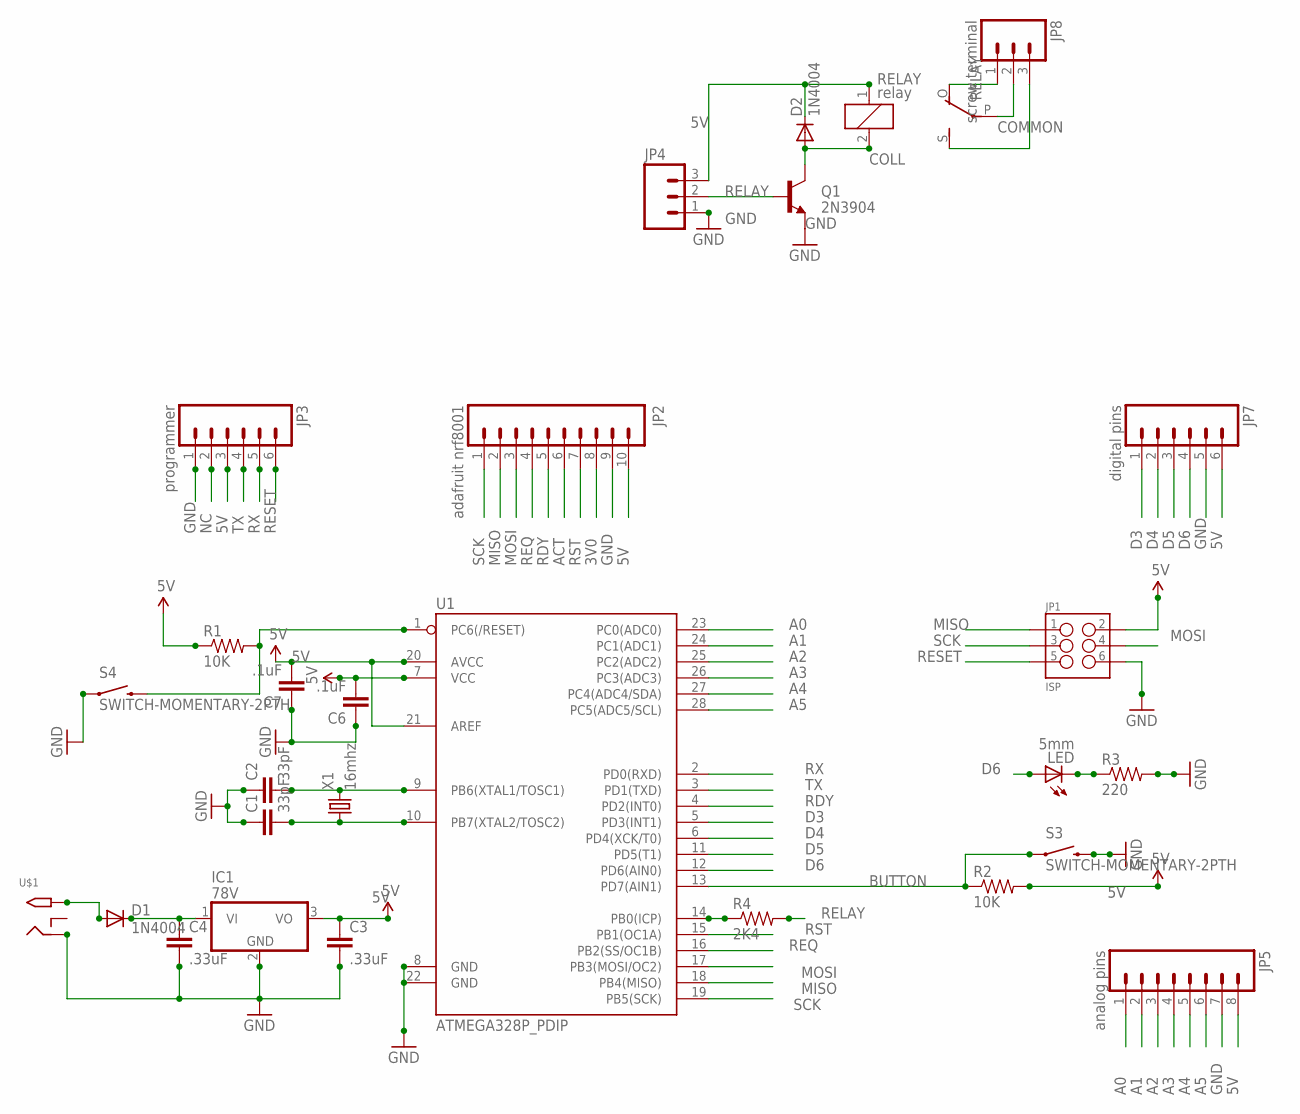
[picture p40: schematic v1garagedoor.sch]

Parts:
C1, C2: 33pF; CAP-PTH-5MM; MOUSER 594-S200K25SL0N63L6R
C3, C4: .33uF; CAP-PTH-SMALL-KIT; MOUSER 810-FK18X5R1A334K
C6, C7: .1uF; CAP-PTH-SMALL-KIT; MOUSER 810-FK18X5R1A334K
D1, D2: 1N4004; DO41-10; MOUSER 621-1N4004
IC1: 78V; TO220V; MOUSER 863-MC7805CTG
JP1: ISP; 2X3-NS; MOUSER 571-5-146252-3
JP2: adafruit nrf8001; 1X10; MOUSER 992-10FX1-254MM
JP3: programmer; 1X06_NO_SILK
JP4: M03LOCK; 1X03_LOCK
JP5: analog pins; 1X08
JP7: digital pins; 1X06_NO_SILK
JP8: screw terminal; SCREWTERMINAL-3.5MM-3
LED: 5mm; LED5MM
Q1: 2N3904; TO-92; MOUSER 610-2N3904
R1, R2: 10K; AXIAL-0.3; MOUSER 603-CFR-25JR-5210K
R3: 220; AXIAL-0.3; MOUSER 603-CFR-25JR-52220R
R4: 2K4; AXIAL-0.3; MOUSER 603-CFR-25JR-52-680R
RELAY: relay; ZF112; MOUSER 655-ORWH-SH105D1F000
S3, S4: SWITCH-MOMENTARY-2PTH; TACTILE-PTH; MOUSER 693-1301.9301
U1: ATMEGA328P_PDIP; DIL28-3; MOUSER 556-ATMEGA328P-PU
U$1: 2.1MMJACKTHM; PJ-102A; MOUSER 992-CON-SOCJ-2155
X1: 16mhz; TC38H; MOUSER 520-160-20-46X

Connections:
3V0: JP2.8
5V: C3.1, C6.2, C7.2, D2.C, IC1.3 (VO), JP1.2, JP2.10, JP3.3, JP4.3, JP5.8, JP7.6, R1.P$1 (1), R2.P$2 (2), RELAY.1, U1.7 (VCC), U1.20 (AVCC), U1.21 (AREF)
12V: D1.A, U$1.TIP
A0: JP5.1, U1.23 (PC0(ADC0))
A1: JP5.2, U1.24 (PC1(ADC1))
A2: JP5.3, U1.25 (PC2(ADC2))
A3: JP5.4, U1.26 (PC3(ADC3))
A4: JP5.5, U1.27 (PC4(ADC4/SDA))
A5: JP5.6, U1.28 (PC5(ADC5/SCL))
ACT: JP2.6
BUTTON: R2.P$1 (1), S3.1, U1.13 (PD7(AIN1))
COLL: D2.A, Q1.3 (C), RELAY.2
COMMON: JP8.2, RELAY.P
D3: JP7.1, U1.5 (PD3(INT1))
D4: JP7.2, U1.6 (PD4(XCK/T0))
D5: JP7.3, U1.11 (PD5(T1))
D6: JP7.4, LED.A, U1.12 (PD6(AIN0))
GND: C1.1, C2.1, C3.2, C4.2, C6.1, C7.1, IC1.2 (GND), JP1.6, JP2.9, JP3.1, JP4.1, JP5.7, JP7.5, Q1.1 (E), R3.P$2 (2), S3.3 (2), S4.1, U1.8 (GND), U1.22 (GND), U$1.RING
MISO: JP1.1, JP2.2, U1.18 (PB4(MISO))
MOSI: JP1.4, JP2.3, U1.17 (PB3(MOSI/OC2))
unnamed: C2.2, U1.9 (PB6(XTAL1/TOSC1)), X1.2
unnamed: C1.2, U1.10 (PB7(XTAL2/TOSC2)), X1.1
unnamed: C4.1, D1.C, IC1.1 (VI)
unnamed: LED.K (C), R3.P$1 (1)
unnamed: JP8.1, RELAY.O
unnamed: JP8.3, RELAY.S
unnamed: R4.P$1 (1), U1.14 (PB0(ICP))
NC: JP3.2
RDY: JP2.5, U1.4 (PD2(INT0))
RELAY: JP4.2, Q1.2 (B), R4.P$2 (2)
REQ: JP2.4, U1.16 (PB2(SS/OC1B))
RESET: JP1.5, JP3.6, R1.P$2 (2), S4.3 (2), U1.1 (PC6(/RESET))
RST: JP2.7, U1.15 (PB1(OC1A))
RX: JP3.5, U1.2 (PD0(RXD))
SCK: JP1.3, JP2.1, U1.19 (PB5(SCK))
TX: JP3.4, U1.3 (PD1(TXD))

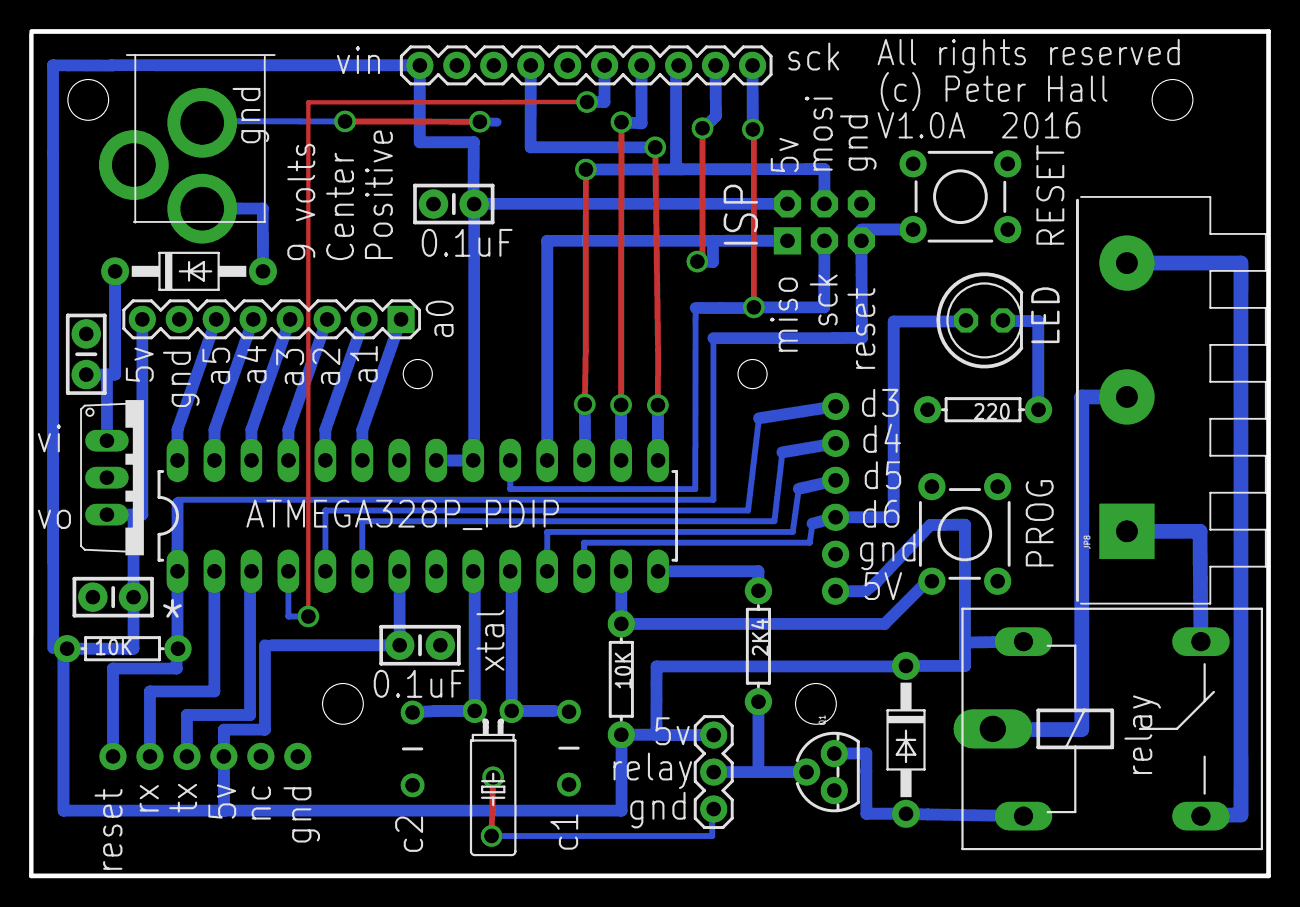
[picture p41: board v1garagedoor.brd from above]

Board: 2 copper layers, 85.0 x 58.0 mm, 28 parts (0 on the bottom side), 33 nets.

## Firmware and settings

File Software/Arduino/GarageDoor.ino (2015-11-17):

// Import libraries (BLEPeripheral depends on SPI)
#include <SPI.h>
#include <BLEPeripheral.h>
#include <MD5.h>
#include <EEPROM.h>

// define pins (varies per shield/board) - these values I've taken from TinySheild_NRF8001_BLE_Example
#define BLE_REQ   10 //
#define BLE_RDY   2 //
#define BLE_RST   9 //
#define LED 6

#define DOORPIN 8 // the relay to activate
#define PASSPIN 7 // button is enable password write.

// eprom
#define eprompasswordposition  0
#define epromlocalnameposition 10

#define dooruuid    "D6BAF795EDAE41E1BED4363B33FA9252"
#define digestuuid  "E1FB481A445B4F3F975B57C36D08821F"
#define ackuuid     "E337E5F0F9A64C369AD8D68056F602A1"
#define newpassword "872519870B484912AB3335086B5183AC"

char  devicepassword[9];                           // this is the device password
char localname[9];  // this is the localname (displays on the iphone app)
char        nonse[9];                                            // this is a generated random nonse
char        hashthisvalue[sizeof(devicepassword) + sizeof(nonse)]; // a place to store the prehash string


// create peripheral instance, see pinouts above
BLEPeripheral     blePeripheral     = BLEPeripheral(BLE_REQ, BLE_RDY, BLE_RST);

BLEService        doorcontroll      = BLEService(dooruuid);

BLECharacteristic switchthing       = BLECharacteristic(dooruuid, BLEWrite, 20);
BLEDescriptor     switchdescriptor  = BLEDescriptor("2901", "MD5");
BLECharacteristic digestnonse       = BLECharacteristic(digestuuid, BLERead, 8);
BLEDescriptor     digestdescriptor  = BLEDescriptor("2901", "nonse");
BLECharacteristic ack               = BLECharacteristic(ackuuid, BLENotify, 8);
BLEDescriptor     ackdescriptor     = BLEDescriptor("2901", "Ack");
BLECharacteristic newpass           = BLECharacteristic(newpassword, BLEWrite, 20);
BLEDescriptor     passdescriptor    = BLEDescriptor("2901", "Password");

//BLEBondStore      store             = BLEBondStore(10);

void setup() {

  Serial.begin(9600);
#if defined (__AVR_ATmega32U4__)
  while (!Serial); // wait for serial
#endif
  pinMode (DOORPIN, OUTPUT);
  pinMode (LED, OUTPUT);
  digitalWrite(LED,HIGH);
  //memset(devicepassword,0,sizeof(devicepass));
  EEPROM.get(eprompasswordposition, devicepassword);
  devicepassword[sizeof(devicepassword)] = '\0';
  EEPROM.get(epromlocalnameposition, localname);
  // cleanup the data - only valid characters
  for (int i = 9; i >= 0 ; i--)
  {
    if (localname[i] < ' ' || localname[i] >= 126 ) localname[i] = '\0';
  }
  // perform a trim
  for (int i = 9; i >= 0 ; i--)
  {
    if (localname[i] == ' ') localname[i] = '\0';
    if (localname[i] != '\0') break;
  }

  if (strlen(localname) == 0) strcpy(localname, "Garage Door");
  Serial.println(localname);
  blePeripheral.setLocalName(localname);
  //store.clearData();
  //blePeripheral.setBondStore(store);

  blePeripheral.setAdvertisedServiceUuid(doorcontroll.uuid());
  // add service and characteristics
  blePeripheral.addAttribute(doorcontroll);
  blePeripheral.addAttribute(switchthing);
  blePeripheral.addAttribute(switchdescriptor);
  blePeripheral.addAttribute(digestnonse);
  blePeripheral.addAttribute(digestdescriptor);
  blePeripheral.addAttribute(ack);
  blePeripheral.addAttribute(ackdescriptor);
  blePeripheral.addAttribute(newpass);
  blePeripheral.addAttribute(passdescriptor);
  // set device name and appearance
  blePeripheral.setDeviceName("RCDO"); // remote controlled door opener
  // https://developer.bluetooth.org/gatt/characteristics/Pages/CharacteristicViewer.aspx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
  blePeripheral.setAppearance(384); // Generic Remote Control

  // begin initialization
  blePeripheral.begin();
  // setup initial password
  randomSeed(analogRead(0)); // set the random sequence - this appears to work reasonably.
  digestnonse.setValue((unsigned char*)getNonse(nonse), 8);

  Serial.println(F("Garage Door - v2"));
  digitalWrite(LED,LOW);
}


void loop() {

  BLECentral central = blePeripheral.central();

  if (central) {

    while (central.connected()) {

      if (newpass.written() )
      {
        if (digitalRead(PASSPIN) == 0) {
          Serial.println("ok");

          int currentpos = 0; // keep track of the string length
          int maxsize = newpass.valueLength() - 1; // need this so we don't overrun
          char *d ;
          char *p = (char*)newpass.value(); // pointer to first character in the data
          memset(localname, 0, sizeof(localname));
          memset(devicepassword, 0, sizeof(devicepassword));
          d = devicepassword; // the destination set to devicepassword
          while (*p && maxsize != 0) {
            if (currentpos++ >= 8) break; // if we reach the max number of characters
            *d++ = *p++;
            maxsize--; // keep track of size
          }
          *d = '\0'; // make sure we terminate the string
          Serial.print("password:"); Serial.println(devicepassword);

          while (*p != '\0' && maxsize != 0 ) {
            *p++;  // need to check we are at the null character, if not advance to the null
            maxsize--;
          }

          *p++; // advance passed the null to the second data part

          currentpos = 0;
          d = localname;  // the destination set to localname
          Serial.print(devicepassword);
          while (*p && maxsize != 0) {
            if (currentpos++ >= 8) break; // if we reach the max number of characters
            *d++ = *p++;
            maxsize--; // keep track of size
          }

          *d++ = '\0'; // make sure we terminate the string.

          //    strncpy(devicepassword,(const char*)newpass.value(),sizeof(devicepassword));
          //    devicepassword[newpass.valueLength()] = '\0';
          // Serial.print("name:"); Serial.println(localname);
          if (strlen(localname) > 0)    {
            EEPROM.put(epromlocalnameposition, localname);
            blePeripheral.setLocalName(localname);
          }
          if (strlen(devicepassword) > 0)   EEPROM.put(eprompasswordposition, devicepassword);



        }
      } else {
        Serial.println("could");
      }
      if (switchthing.written() && switchthing.valueLength() == 16) {

        // build the string we need to calc a hash value for
        strcpy(hashthisvalue, devicepassword);
        strcat(hashthisvalue, nonse);

        unsigned char* hash = MD5::make_hash(hashthisvalue);
        //dont' forget to Give the Memory back to the System
        Serial.println("*****");
        Serial.println((char*)hash);
        Serial.println("***");
        Serial.println((char*)switchthing.value());

        // check it's what we are expecting
        if (memcmp((const char*)hash, (const char*)switchthing.value(), 16) == 0) {
          digitalWrite(DOORPIN, HIGH);       // Turn relay 1 on
          delay(1000);                      // Wait 1 second
          digitalWrite(DOORPIN, LOW);        // Turn relay 1 off

          // at the end of the activate get ready , setup a new password.
          digestnonse.setValue((unsigned char*)getNonse(nonse), 8);
          ack.setValue((const unsigned char*)"Success", 7);

        } else {
          ack.setValue((const unsigned char*)"Fail", 4);
        } // if memcmp


        free(hash);

      } // if switchthing written
    } // while connected
  } // central
} // loop


// produce a random nonse - in the ascii character range 33 to 126, which are visible glyphs
char *getNonse(char *pw)
{

  for (int indx = 0; indx < 8; indx++)
  {
    pw[indx] = (char)random(33, 126);
  }
  pw[8] = 0;
  return (pw);
}

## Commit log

2015-11-17 initial commit, I hope I have everything
    [v1garagedoor.brd, v1garagedoor.sch]
2015-11-18 playing with the housing
2015-11-25 still working on the housing, added some accessibility holes, to access the power screws. resized the mount holes.
2015-11-26 still working on the housing, added a spring to the push button, made some changes to the button design.
2015-12-03 changes to the housing
    [pushbutton_limiter.stl]
2015-12-07 some changes to the housing started on the documentation
    [BOM.xlsx]
2015-12-21 added some documentation made some changes to the board layout because of the v1 board has some needed changes. I expect there to be a few more changes, around the silkscreen output
    [BOM.xlsx, v1garagedoor.brd, v1garagedoor.sch]
2016-02-15 just updating the repo
    [BOM.xlsx, v1garagedoor.brd, v1garagedoor.sch]

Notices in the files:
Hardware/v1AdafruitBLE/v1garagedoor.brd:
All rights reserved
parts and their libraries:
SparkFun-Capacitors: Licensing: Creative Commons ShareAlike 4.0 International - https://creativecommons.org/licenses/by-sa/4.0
